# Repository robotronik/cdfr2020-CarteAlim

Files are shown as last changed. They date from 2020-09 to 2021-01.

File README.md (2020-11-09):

# Carte alimentation du robot 2020

- [Carte alimentation du robot 2020](#carte-alimentation-du-robot-2020)
  - [Changelog](#changelog)
    - [Commits](#commits)
    - [Versions du projet](#versions-du-projet)
  - [Protection de la batterie](#protection-de-la-batterie)
    - [Protection contre la décharge](#protection-contre-la-décharge)
    - [Protection contre une inversion de la polarité](#protection-contre-une-inversion-de-la-polarité)
  - [Les sorties](#les-sorties)
    - [Partie commande](#partie-commande)
    - [Partie actionneurs](#partie-actionneurs)
    - [Table des fusibles](#table-des-fusibles)
  - [Taille des pistes](#taille-des-pistes)

## Changelog
### Commits
|Date|Nom du commit|Version du projet|
|---|---|---|
| 26/10/2020 | Fin du schema et routage
| 26/10/2020 | Changement pour ajouter la possibiliter de court circuiter les 2 buzzers ou 1|v1
| 27/10/2020 | Readme propre | Ajout du README
| 27/10/2020 | Sans regul moteurs et fix du reste |v2 bis 
| 10/11/2020 | Avec regul moteurs et texte sur autre couche | v2 (avec plan de masse)

### Versions du projet
|Version|Description|
|---|---|
|v1| Le routage est fait avec 0.5mm partout, pas de plan de masse, mauvaise empreinte pour le transistor, mauvais noms de sorties (n'indiquent pas clairement la tension)|
|v2 *| Largeur de piste tenant compte de l'intensité pouvant passer, bonne empreinte du transistor, bons noms de sortie
|v2 bis| Sorties moteurs dérégulées : elles sont "directement" reliées à la batterie|

## Protection de la batterie

### Protection contre la décharge

*Repose sur le modèle présenté dans cette vidéo : www.youtube.com/watch?v=1Fs4SfVSsLk*\
Un bipper de batterie est relié à la carte.\
Ses buzzers sont remplacés par un relais qui coupe la partie négative de la batterie (celle-ci ne peut donc plus se décharger).\
Attention le relais prévu a une alimentation de 5V max, il y a donc possibilité de mettre un pont diviseur de tension ou une diode (si cela suffit) pour réduire la tension aux bornes de Coil2 (celle issu\

><u>__/!\\__</u> Lors du branchement de la batterie, le bipper "bip" usuellement, ici ça se traduit par une coupure du relais. Il faut réactiver l'utilisation de la batterie.<br>
>**Pour réactiver l'utilisation de la batterie** : 
>- S'assurer qu'elle est chargée à un niveau suffisant
>- Appuyer sur le bouton SW1 (reset du relais)

### Protection contre une inversion de la polarité

On a un PMOS en reverse polarity protection.\
Fait-il office de protection contre les surcharges ? (à la place d'un fusible)

## Les sorties

### Partie commande

*Celle-ci est liée au SW_Starter qui est l'emplacement où devra être installée la tirette de démarrage.*

### Partie actionneurs

*Puisque le bouton d'arrêt d'urgence doit arrêter tout mouvement du robot, celui-ci n'est relié qu'à la partie actionneurs.*

### Table des fusibles
|Sortie |Fusible (valeur estimée approximativement)|
|--- |---|
|Cmd-5V | 1A  |
|Cmd-7V5 | 1A  |
|Motor1-12V | 2A  |
|Motor1-12V | 2A  |
|Actuator-5V | 2A  |

## Taille des pistes
*https://www.digikey.com/en/resources/conversion-calculators/conversion-calculator-pcb-trace-width*

*https://www.mclpcb.com/pcb-trace-width-vs-current-table/*

|Zone |Courant max /A|Taille estimée /mm|
|--- |---|---|
|Cmd-5V |1 | 0.25
|Cmd-7V5 |1 | 0.25
|Motor1-18V |2 | 0.76
|Motor2-18V |2 | 0.76
|Actuator-5V |2 | 0.76
|All active |6 | 3.81
|BatteryIn-18V  |8 | 5.59

$$
I_{max-battery}= \sum{I_{max-Zone-i}}
$$

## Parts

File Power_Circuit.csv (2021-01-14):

Id | Référence | Boîtier | Quantité | Désignation | Fournisseur et réf
1 | U2,U9,U8,U10,U3 | DC_DC_LM2596_small | 5 | DSN2596 | Version tout en un sur une plaque pcb (pas vraiment un boitier)
2 | Q1 | TO-252-3_TabPin2 | 1 | IRF7606PBF_3PINS_BWOUF
3 | R4,R9,R8,R1,R2,R3,R5,R6 | R_1206_3216Metric_Pad1.42x1.75mm_HandSolder | 8 | R
4 | J2 | PinHeader_1x04_P2.54mm_Vertical | 1 | Conn_01x04
5 | BZ2,BZ1 | Buzzer_12x9.5RM7.6 | 2 | Buzzer
6 | U5 | PhoenixContact_MCV_1,5_2-G-3.81_1x02_P3.81mm_Vertical | 1 | B_Plug_E-Stop_out
7 | U4 | PhoenixContact_MCV_1,5_2-G-3.81_1x02_P3.81mm_Vertical | 1 | B_Plug_E-Stop_In
8 | K1 | DSP1AL2DC5V | 1 | DSP1A-L2-DC5V
9 | U13 | PhoenixContact_MCV_1,5_2-G-3.81_1x02_P3.81mm_Vertical | 1 | B_Plug_5v_Actuator
10 | U12 | PhoenixContact_MCV_1,5_2-G-3.81_1x02_P3.81mm_Vertical | 1 | B_Plug_18v_Motor2
11 | U11 | PhoenixContact_MCV_1,5_2-G-3.81_1x02_P3.81mm_Vertical | 1 | B_Plug_18v_Motor1
12 | U7 | PhoenixContact_MCV_1,5_2-G-3.81_1x02_P3.81mm_Vertical | 1 | B_Plug_7v5_Command
13 | U6 | PhoenixContact_MCV_1,5_2-G-3.81_1x02_P3.81mm_Vertical | 1 | B_Plug_5V_Command
14 | U1 | PhoenixContact_MCV_1,5_2-G-3.81_1x02_P3.81mm_Vertical | 1 | B_Plug_Battery_In
15 | C1 | C_1206_3216Metric_Pad1.42x1.75mm_HandSolder | 1 | C
16 | C2 | C_1206_3216Metric_Pad1.42x1.75mm_HandSolder | 1 | CP
17 | D1,D3,D4,D5,D6,D7 | LED_1206_3216Metric_Pad1.42x1.75mm_HandSolder | 6 | LED
18 | D8 | LED_1206_3216Metric_Pad1.42x1.75mm_HandSolder | 1 | 10V
19 | F1,F2,F3,F4,F5,F6 | Fuse_1210_3225Metric_Pad1.42x2.65mm_HandSolder | 6 | Fuse
20 | J1 | PinSocket_1x09_P2.54mm_Horizontal | 1 | Conn_01x09
21 | R7 | R_1206_3216Metric_Pad1.42x1.75mm_HandSolder | 1 | 10k
22 | SW1 | R_Axial_DIN0207_L6.3mm_D2.5mm_P10.16mm_Horizontal | 1 | SW_Push | un interrupteur

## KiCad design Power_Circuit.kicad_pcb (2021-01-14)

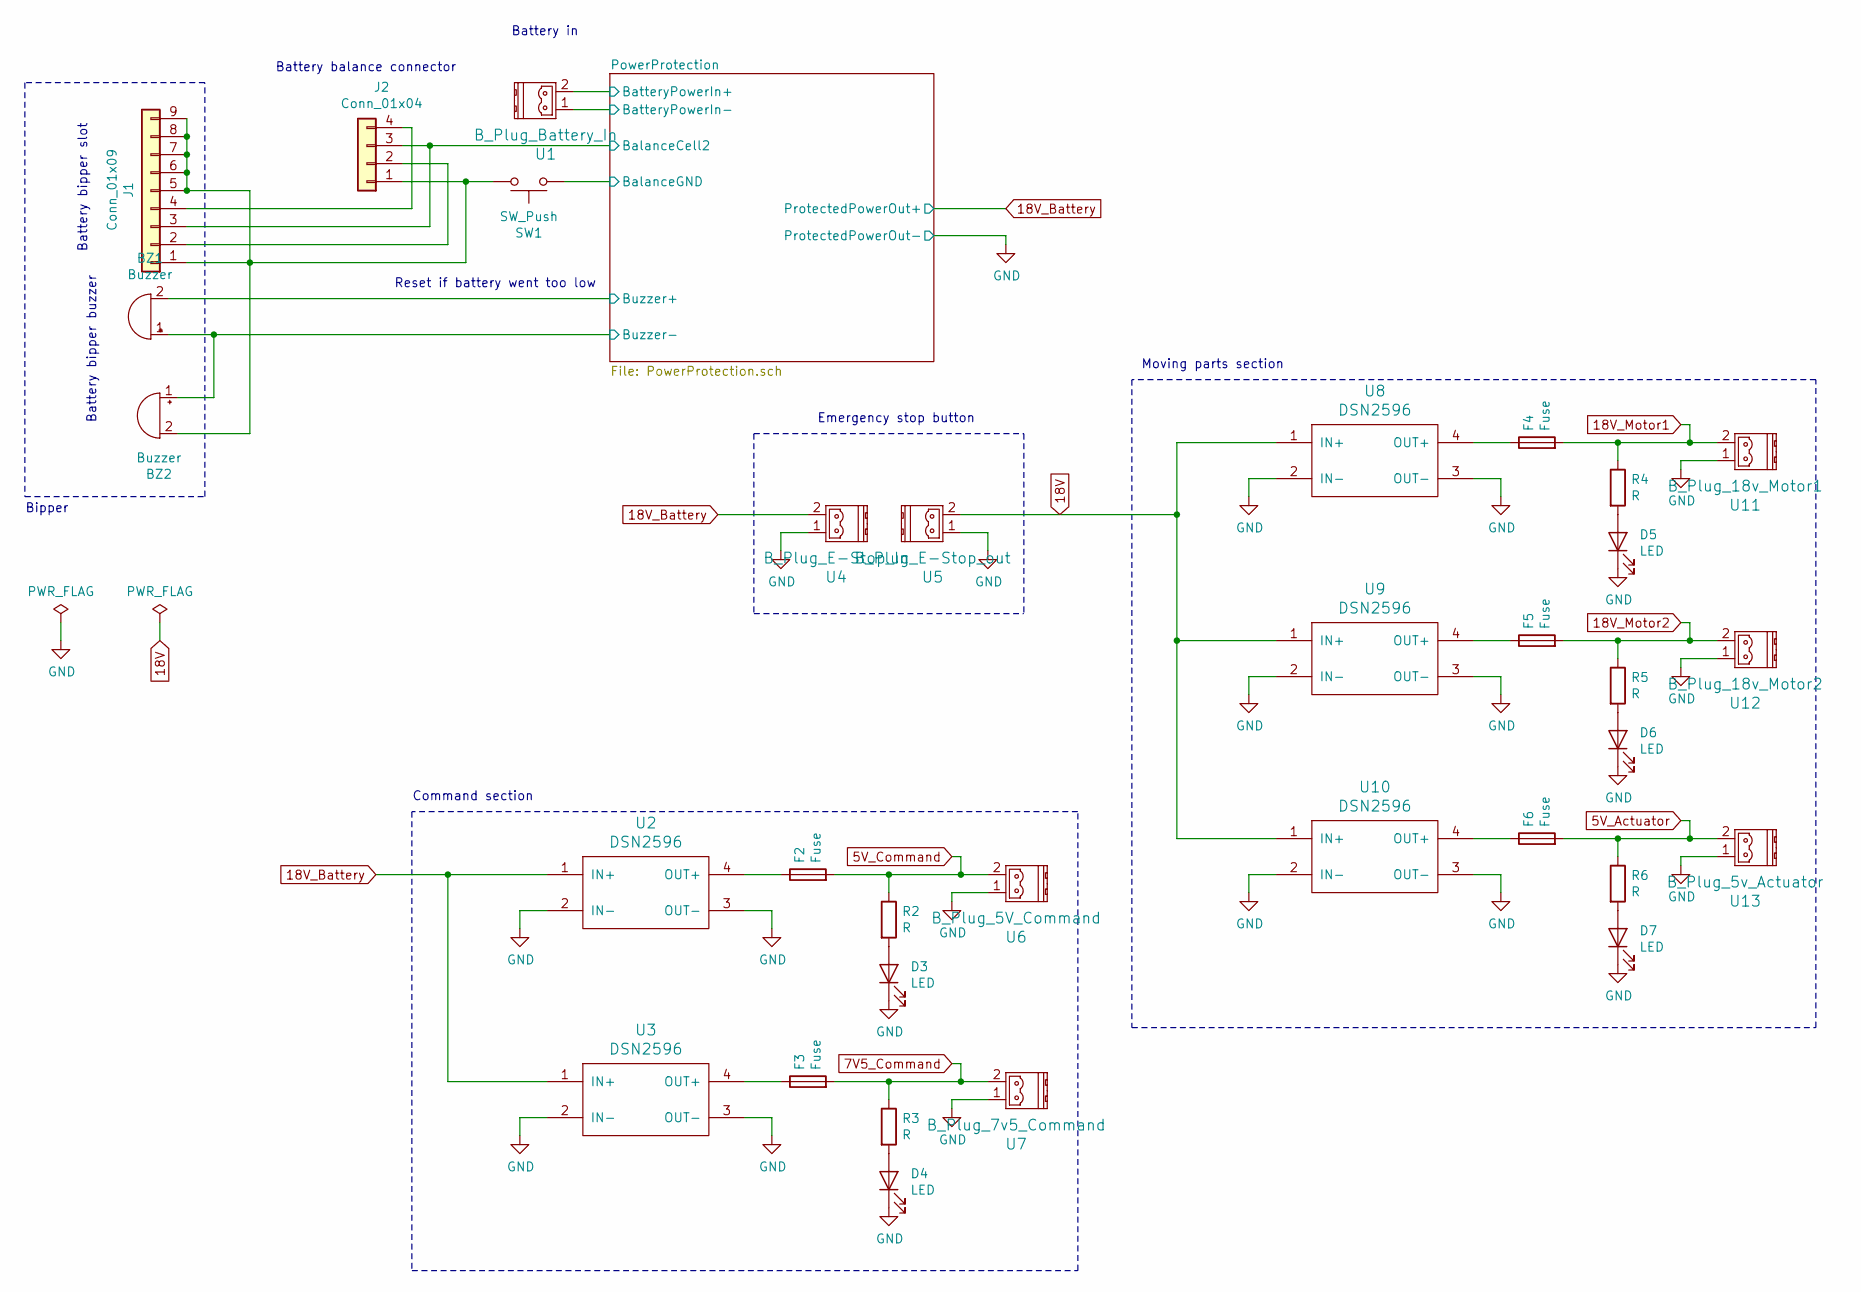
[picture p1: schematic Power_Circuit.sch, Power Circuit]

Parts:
BZ1, BZ2: Buzzer; Buzzer_12x9.5RM7.6
D3, D4, D5, D6, D7: LED; LED_1206_3216Metric_Pad1.42x1.75mm_HandSolder
F2, F3, F4, F5, F6: Fuse; Fuse_1210_3225Metric_Pad1.42x2.65mm_HandSolder
J1: Conn_01x09; PinSocket_1x09_P2.54mm_Horizontal
J2: Conn_01x04; PinHeader_1x04_P2.54mm_Vertical
R2, R3, R4, R5, R6: R; R_1206_3216Metric_Pad1.42x1.75mm_HandSolder
SW1: SW_Push; R_Axial_DIN0207_L6.3mm_D2.5mm_P10.16mm_Horizontal
U1: B_Plug_Battery_In; PhoenixContact_MCV_1,5_2-G-3.81_1x02_P3.81mm_Vertical
U2, U3, U8, U9, U10: DSN2596; DC_DC_LM2596_small
U4: B_Plug_E-Stop_In; PhoenixContact_MCV_1,5_2-G-3.81_1x02_P3.81mm_Vertical
U5: B_Plug_E-Stop_out; PhoenixContact_MCV_1,5_2-G-3.81_1x02_P3.81mm_Vertical
U6: B_Plug_5V_Command; PhoenixContact_MCV_1,5_2-G-3.81_1x02_P3.81mm_Vertical
U7: B_Plug_7v5_Command; PhoenixContact_MCV_1,5_2-G-3.81_1x02_P3.81mm_Vertical
U11: B_Plug_18v_Motor1; PhoenixContact_MCV_1,5_2-G-3.81_1x02_P3.81mm_Vertical
U12: B_Plug_18v_Motor2; PhoenixContact_MCV_1,5_2-G-3.81_1x02_P3.81mm_Vertical
U13: B_Plug_5v_Actuator; PhoenixContact_MCV_1,5_2-G-3.81_1x02_P3.81mm_Vertical

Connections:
5V_Actuator: F6.2, R6.1, U13.2
5V_Command: F2.2, R2.1, U6.2
7V5_Command: F3.2, R3.1, U7.2
18V: U5.2, U8.1 (IN+), U9.1 (IN+), U10.1 (IN+)
18V_Battery: U2.1 (IN+), U3.1 (IN+), U4.2; also elsewhere on the board
18V_Motor1: F4.2, R4.1, U11.2
18V_Motor2: F5.2, R5.1, U12.2
/PowerProtection/BalanceCell2: J1.3, J2.3; also elsewhere on the board
/PowerProtection/BalanceGND: SW1.1; also elsewhere on the board
/PowerProtection/BatteryPowerIn+: U1.2; also elsewhere on the board
/PowerProtection/BatteryPowerIn-: U1.1; also elsewhere on the board
/PowerProtection/Buzzer+: BZ1.2 (+); also elsewhere on the board
/PowerProtection/Buzzer-: BZ1.1 (-), BZ2.1 (-); also elsewhere on the board
GND: D3.1 (K), D4.1 (K), D5.1 (K), D6.1 (K), D7.1 (K), U2.2 (IN-), U2.3 (OUT-), U3.2 (IN-), U3.3 (OUT-), U4.1, U5.1, U6.1, U7.1, U8.2 (IN-), U8.3 (OUT-), U9.2 (IN-), U9.3 (OUT-), U10.2 (IN-), U10.3 (OUT-), U11.1, U12.1, U13.1; also elsewhere on the board
unnamed: BZ2.2 (+), J1.1, J1.5, J1.6, J1.7, J1.8, J1.9, J2.1, SW1.2
unnamed: D3.2 (A), R2.2
unnamed: D4.2 (A), R3.2
unnamed: D5.2 (A), R4.2
unnamed: D6.2 (A), R5.2
unnamed: D7.2 (A), R6.2
unnamed: F2.1, U2.4 (OUT+)
unnamed: F3.1, U3.4 (OUT+)
unnamed: F4.1, U8.4 (OUT+)
unnamed: F5.1, U9.4 (OUT+)
unnamed: F6.1, U10.4 (OUT+)
unnamed: J1.2, J2.2
unnamed: J1.4, J2.4

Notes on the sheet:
Battery in
Moving parts section
Command section
Emergency stop button
Battery bipper slot
Battery balance connector
Battery bipper buzzer
Reset if battery went too low
Bipper

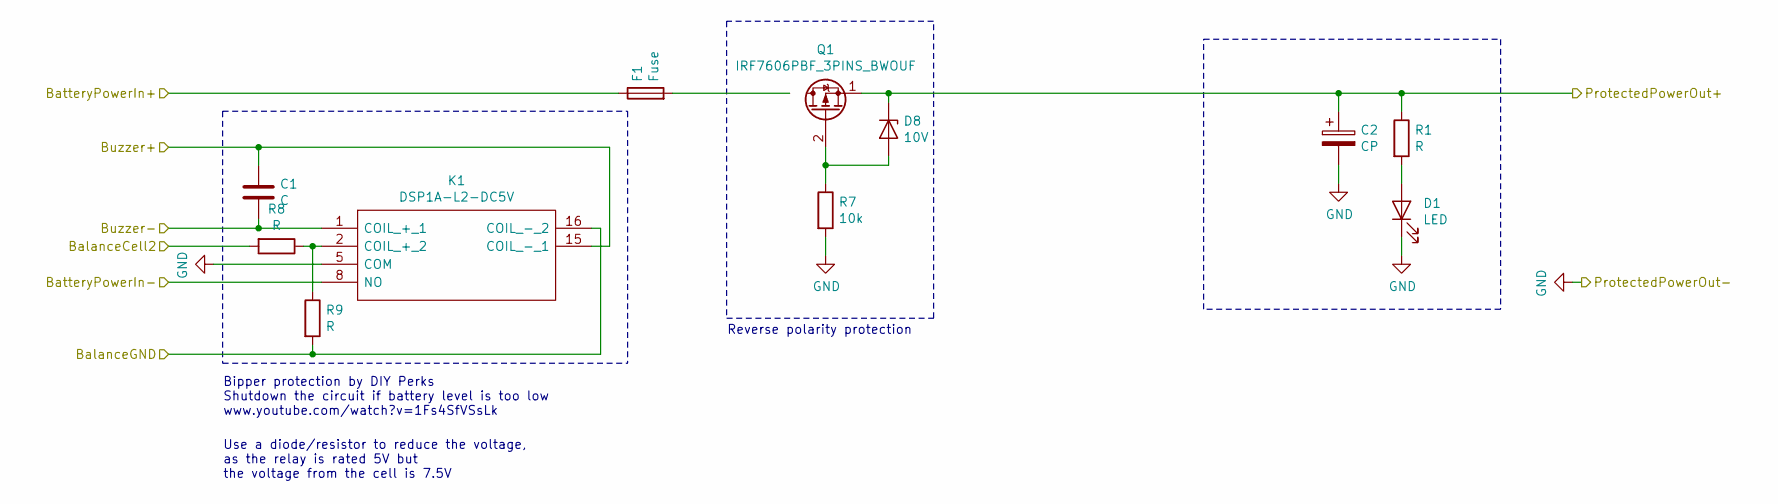
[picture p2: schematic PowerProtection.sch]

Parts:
C1: C; C_1206_3216Metric_Pad1.42x1.75mm_HandSolder
C2: CP; C_1206_3216Metric_Pad1.42x1.75mm_HandSolder
D1: LED; LED_1206_3216Metric_Pad1.42x1.75mm_HandSolder
D8: 10V; LED_1206_3216Metric_Pad1.42x1.75mm_HandSolder
F1: Fuse; Fuse_1210_3225Metric_Pad1.42x2.65mm_HandSolder
K1: DSP1A-L2-DC5V; DSP1AL2DC5V; Mouser Part Number 769-DSP1A-L2-DC5V
Q1: IRF7606PBF_3PINS_BWOUF; TO-252-3_TabPin2
R1, R8, R9: R; R_1206_3216Metric_Pad1.42x1.75mm_HandSolder
R7: 10k; R_1206_3216Metric_Pad1.42x1.75mm_HandSolder

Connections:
18V_Battery: C2.1, D8.1 (K), Q1.1 (S), R1.1; also elsewhere on the board
/PowerProtection/BalanceCell2: R8.2; also elsewhere on the board
/PowerProtection/BalanceGND: K1.16 (COIL_-_2), R9.2; also elsewhere on the board
/PowerProtection/BatteryPowerIn+: F1.1; also elsewhere on the board
/PowerProtection/BatteryPowerIn-: K1.8 (NO); also elsewhere on the board
/PowerProtection/Buzzer+: C1.1, K1.15 (COIL_-_1); also elsewhere on the board
/PowerProtection/Buzzer-: C1.2, K1.1 (COIL_+_1); also elsewhere on the board
GND: C2.2, D1.1 (K), K1.5 (COM), R7.2; also elsewhere on the board
unnamed: D1.2 (A), R1.2
unnamed: D8.2 (A), Q1.2 (G), R7.1
unnamed: F1.2, Q1.3 (D)
unnamed: K1.2 (COIL_+_2), R8.1, R9.1

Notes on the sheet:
Bipper protection by DIY Perks Shutdown the circuit if battery level is too low www.youtube.com/watch?v=1Fs4SfVSsLk
Reverse polarity protection
Use a diode/resistor to reduce the voltage, as the relay is rated 5V but the voltage from the cell is 7.5V

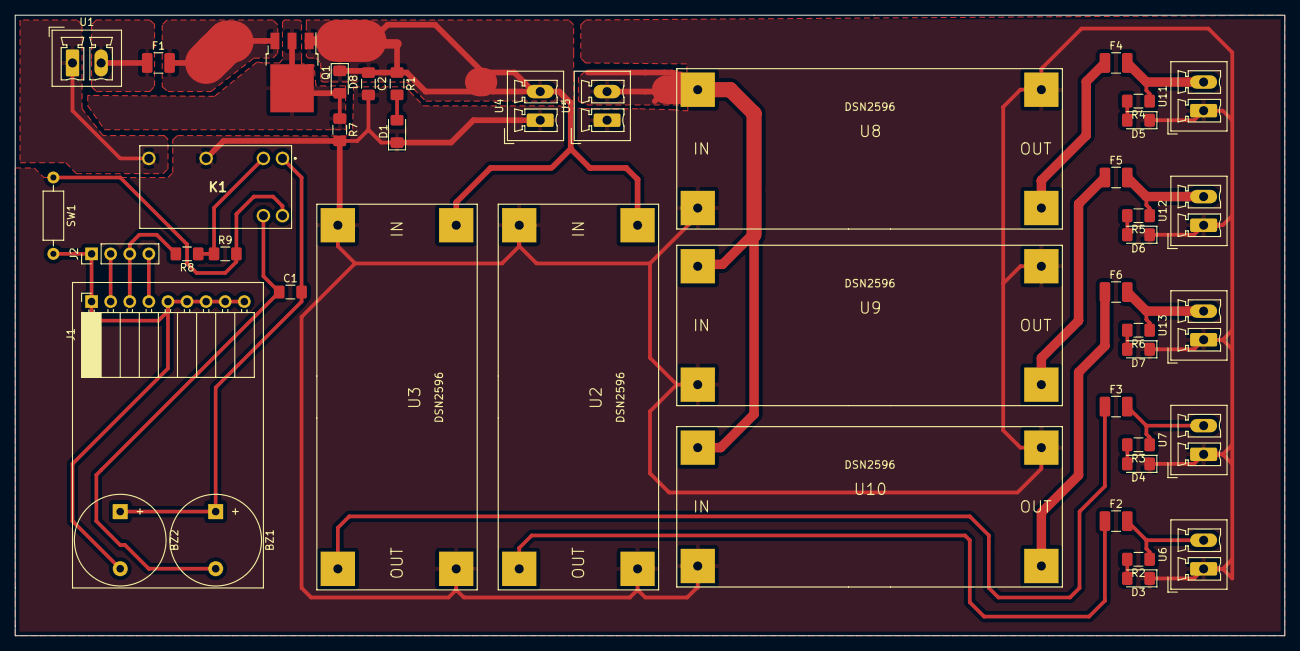
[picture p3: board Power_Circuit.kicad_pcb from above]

Board: 2 copper layers, 168.9 x 82.6 mm, 44 parts (0 on the bottom side), 31 nets.

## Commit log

2020-09-05 Schema sans protection batterie
    [Power_Circuit.kicad_pcb, Power_Circuit.sch]
2020-09-06 Ajout du schéma
    Sans protection réelle de la batterie
    [Power_Circuit.kicad_pcb, Power_Circuit.sch]
2020-10-15 Nouvelle avancee, manque la protection reverse polarity
    [PowerProtection.sch, Power_Circuit.sch, XavProtec.sch]
2020-10-15 Il reste a trouver empreintes et router
    [PowerProtection.sch, Power_Circuit.sch, XavProtec.sch]
2020-10-15 ajout de la tirette
    [PowerProtection.sch, Power_Circuit.sch]
2020-10-26 Fin du schema et routage
    [PowerProtection.sch, Power_Circuit.sch, cdfr2020revpolprot.kicad_pcb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]
2020-10-26 Changement pour ajouter la possibiliter de court circuiter les 2 buzzers ou 1
    [Power_Circuit.kicad_pcb, Power_Circuit.sch]
2020-11-09 Avec regul moteur et texte sur autre couche
    [PowerProtection.sch, Power_Circuit.kicad_pcb, Power_Circuit.sch]
2021-01-14 Ajout BOM, suppression tirette, correction silk, correction des plans pour meilleur refroidissement du transistor notamment
    [Power_Circuit.csv, Power_Circuit.kicad_pcb, Power_Circuit.sch]
2021-01-14 Changement de la liste a acheter, jaune = important et probablement pas au local
    [Power_Circuit.csv, Power_Circuit.xls]
2021-01-14 apres fermeture il restait ce fichier
